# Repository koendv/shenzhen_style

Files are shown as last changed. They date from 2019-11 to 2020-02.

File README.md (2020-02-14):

# Shenzhen style

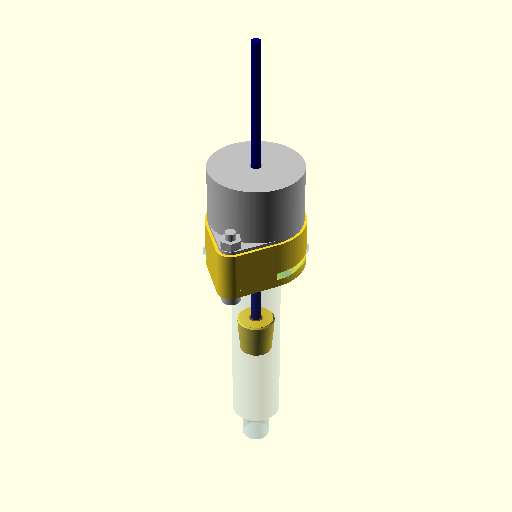
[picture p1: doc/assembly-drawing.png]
 

A 10cc glue dispenser. Designed to have a low number of pieces. Simple to solder, and easy to assemble. Plungers for [10cc Chinese generic](https://www.google.com/search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) , and 10cc Nordson. Adapter for mounting the glue dispenser on a CNC 3018 router.

Cutout view of the assembled dispenser: [3D assembly view](stl/assembly.stl)

## Bill of Materials
### 3D-Printed Workpieces
Workpieces printed in ABS using FDM:

- [body](stl/body.stl)
- [syringe holder](stl/syringe_holder.stl)
- [adapter for cnc 3018](stl/cnc3018_adapter.stl)
- [plunger](stl/plunger.stl)
- [insert_practice](stl/insert_practice.stl)

Leave part orientation as is when imported into PrusaSlicer. Designed to print without support.

### Dispenser Bill of materials

Quantity|Item
--------|----
1|[Robotdigg NC35-BYZ-120](https://www.robotdigg.com/product/1147/12V-35-captive-or-non-captive-linear-pm-stepper-motor) non-captive linear stepper, 7.5°/step
1|[M3 x 5.0mm O.D. x 6.0mm L threaded knurled brass insert](https://www.aliexpress.com/item/4000232858343.html)
2|[M4x25mm screw](https://www.aliexpress.com/item/4000197066058.html)
2|[M4 nut](https://www.aliexpress.com/item/32959149109.html)

Of course, you'll also need syringes. Some products, such as [Mechanic brand solder paste](https://www.google.com/search?q=Mechanic+XG-Z40+10cc+Syringe+Solder+Paste+Flux+Paste+Sn63%2FPb37), are sold in syringes, Luer needle included, ready to use. Or you can buy empty [10cc industrial glue dispenser syringes](https://www.aliexpress.com/item/33025919381.html) and fill them yourself.

## Assembly
- Set your soldering iron to the filament extrusion temperature used during 3D printing, about 255°C for ABS.
- As a test, take the workpiece [insert_practice](stl/insert_practice.stl) and place 4 heat-set inserts. 
- Put an M3 threaded brass insert in the [plunger](stl/plunger.stl).
- Screw the plunger on the stepper motor shaft.
### Hand-held
For the hand-held dispenser:
- Put the syringe in the [syringe holder](stl/syringe_holder.stl)
- Join stepper motor, [body](stl/body.stl), and syringe holder with the M4x25 screws.
- Connect the glue dispenser stepper motor to the controller board.

### CNC 3018 adapter
For the dispenser mounted in a CNC 3018 z-carriage:
- Put the syringe in the [adapter for cnc 3018](stl/cnc3018_adapter.stl).
- Join stepper motor, [body](stl/body.stl), and cnc 3018 adapter with the M4x25 screws.
- Put the dispenser in the CNC 3018 z-carriage. The dispenser has the same diameter as the router spindle, 42mm. Tighten the screws of the z-carriage very lightly, or not at all.
- Connect the glue dispenser stepper to the 3d-printer controller extruder (E0/E1).
- Dispensing glue is done by printing a g-code file, like a 3d printer.

## Controller
The controller is only needed if you wish to use the glue dispenser as a stand-alone, hand-held device. 

[Schematic and board layout at easyeda](http://easyeda.com/koendv/stepper-controller).

Quantity|Item
--------|----
1|[PCB](https://jlcpcb.com/)
1|[STM32F103C8T6 Blue Pill](http://www.aliexpress.com/item/32981849126.html)
1|[TMC2130 Silent Stepstick](https://www.aliexpress.com/item/32970150483.html)
1|[Mini dc-dc converter 24V to 5v](https://www.aliexpress.com/item/32796268715.html)
1|[0.96inch 128X64 I2C SSD1306 OLED WHITE/BLUE](https://www.aliexpress.com/item/32830523451.html)
1|[EC11 Rotary Encoder with Button](https://www.aliexpress.com/item/32915420023.html)
1|[3.5mm headphone jack](https://www.aliexpress.com/item/4000309078079.html)
1|[DC005 DC Power Jack 5.5mm dia, 2.5mm pin](https://www.aliexpress.com/item/4000034340966.html)
2|Pushbutton 6x6mm
1|Capacitor 47u/50V
1|4-Pin Male header (Dupont or JST XH-4AK)

*This is Work In Progress.*

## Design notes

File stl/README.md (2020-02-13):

3d-print the following files:

- [body](body.stl)
- [syringe holder](syringe_holder.stl)
- [plunger](plunger.stl)

If your cnc 3018 has a 45mm spindle, print this adapter:
- [adapter for mounting on cnc3018](cnc3018_adapter.stl)

If your cnc 3018 has a 52mm spindle, print this adapter:
- [adapter for mounting on cnc3018 with 52mm spindle](cnc3018_adapter_52mm.stl)

If you wish to practice threaded inserts first, also print:

- [insert practice](insert-practice.stl)

The directory also contains the following files:

- [assembly](assembly.stl) assembled hand-held dispenser

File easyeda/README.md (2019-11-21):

# PCB

pcb top pcb bottom 

[Gerber files](https://github.com/koendv/shenzhen_style/raw/master/easyeda/Gerber_stepper%20controller.zip) ready for pcb manufacturing. 

PCB project at [https://easyeda.com/koendv/stepper-controller](https://easyeda.com/koendv/stepper-controller)

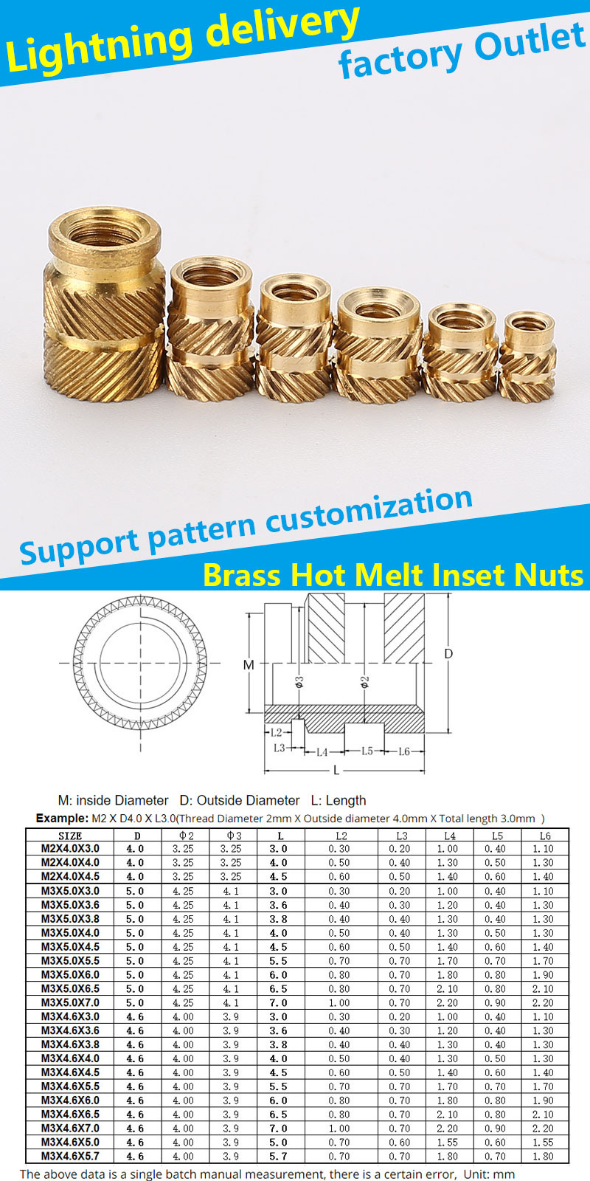
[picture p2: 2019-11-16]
doc/aliexpress-4000232858343.jpg

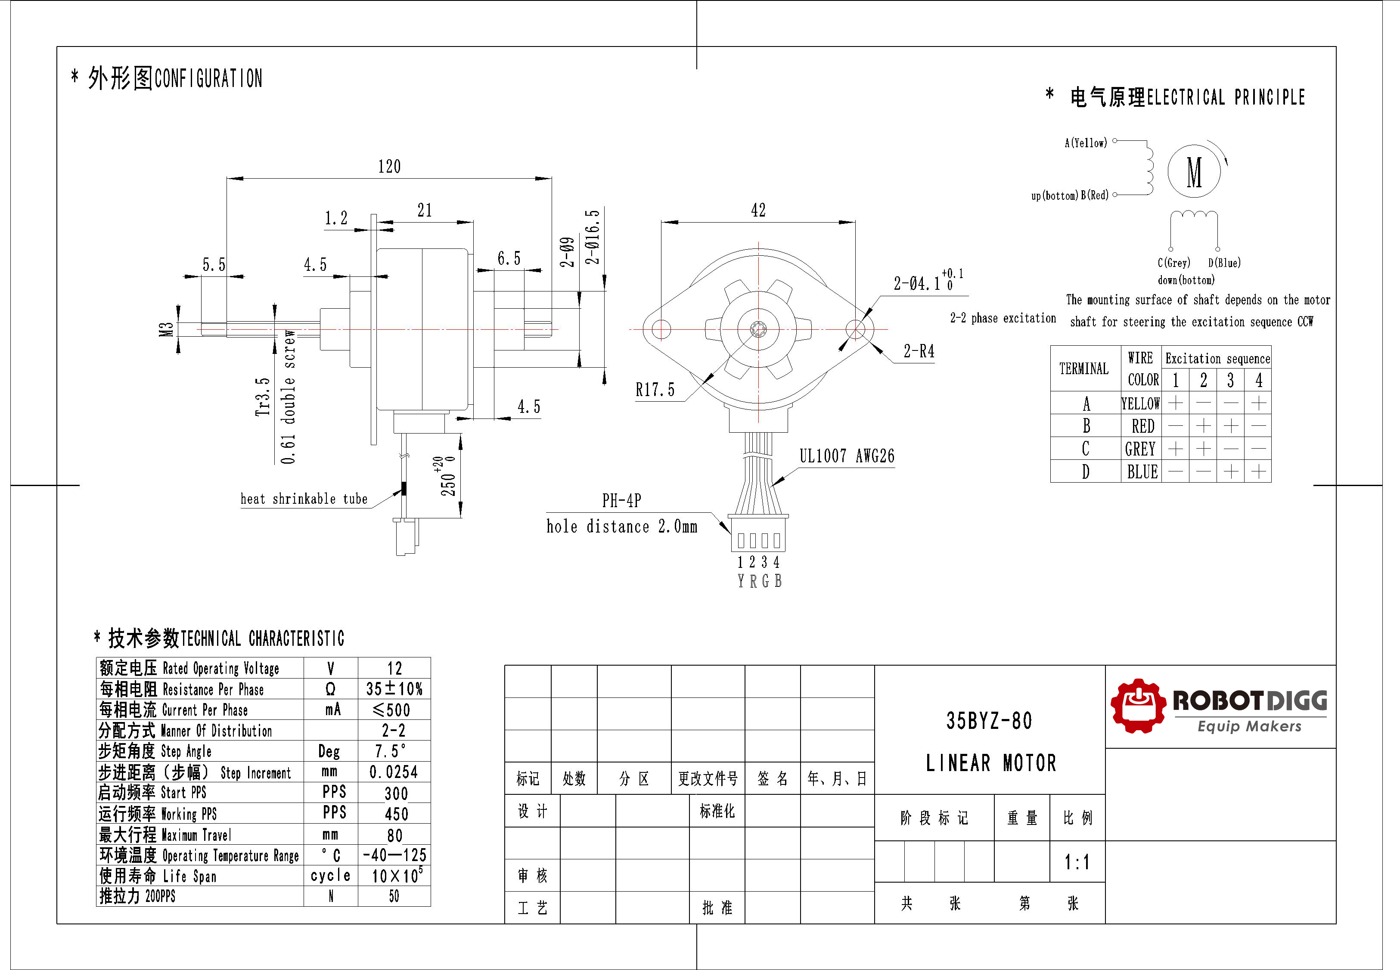
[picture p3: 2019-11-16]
doc/robotdigg-35-BYZ.jpeg

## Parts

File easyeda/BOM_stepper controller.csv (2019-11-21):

ID | Name | Designator | Footprint | Quantity | Manufacturer Part | Manufacturer | Supplier | Supplier Part
1 | Button-6x6x6mm | SW2,SW3 | SW-TH_4PIN-L6.00-W6.00 | 2 | Switch,6*6*6Plastic head,260G, 0.25mm,Straight line | BBJ | LCSC | C71836
2 | 0.96 128X64 I2C SSD1306 OLED WHITE/BLUE | U2 | 0.96 128X64 I2C SSD1306 OLED WHITE/BLUE | 1 | OLED 4PIN | WAVGAT | Aliexpress | 32830523451
3 | 47u/50V | C1 | CAP-D8.0XF3.5 | 1
4 | 3.5mm headphone jack | J1 | AUDIO-PJ320 | 1 | PJ320 headphone jack | BOOMELE | Aliexpress | 4000309078079
5 | MINI DC-DC CONVERTER 12-24V TO 5V 3A MAX | U3 | MINI DC-DC CONVERTER 12-24V TO 5V 3A MAX | 1 | QS-1205CME-3A | QSKJ | Aliexpress | 32796268715
6 | DC005 DC Power Jack 5.5mm dia, 2.5mm pin | P1 | DC005-2.5MM | 1 | Three-pin power interface DC005 2.5MMsocket Bagged RHOS | ReliaPro | Aliexpress | 4000034340966
7 | PWR_OFF | JP1 | 1X02 | 1
8 | TMC2130 stepstick | U1 | TMC2130 STEPSTICK \W DIAG0 DIAG1 VREF | 1 | TMC2130 stepstick |  | Aliexpress | 32970150483
9 | XH-4AK M | CN1 | XH-4A | 1 | - | Boom Precision Elec | LCSC | C146106
10 | STM32F103C8T6 BLUEPILL | U4 | STM32F103C8T6 BLUEPILL | 1 |  |  | Aliexpress | 32981849126
11 | EC11 Button | SW1 | EC11B-V | 1 | EC111012010H | Alps | Aliexpress | 32915420023

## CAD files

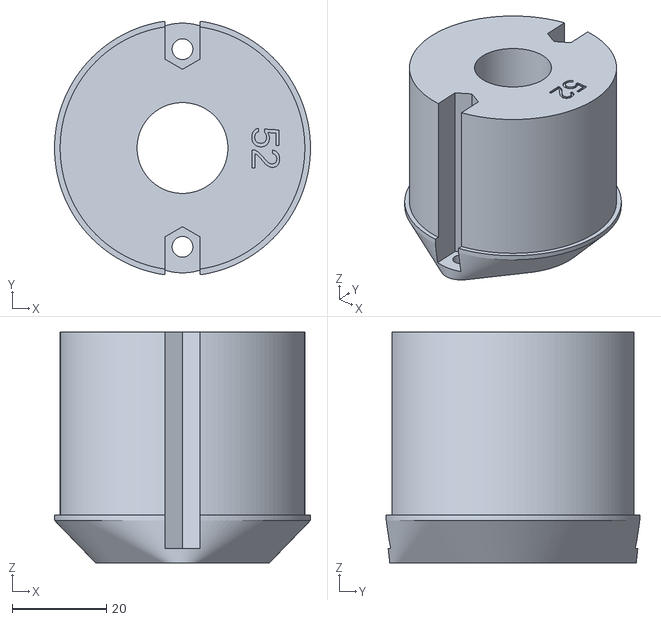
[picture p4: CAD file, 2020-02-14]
stl/cnc3018_adapter_52mm.stl
54.4 x 53.9 x 49.0

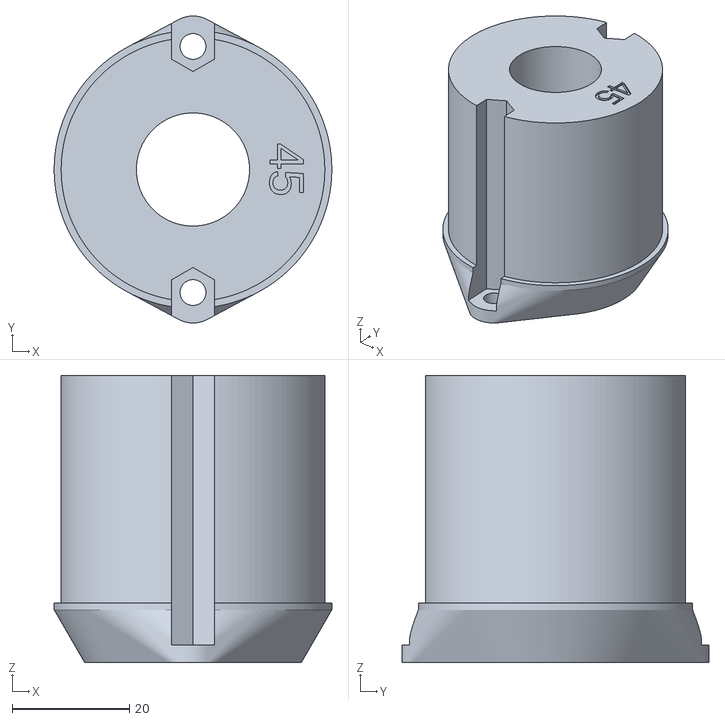
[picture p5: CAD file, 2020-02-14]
stl/cnc3018_adapter.stl
47.4 x 52.4 x 49.0

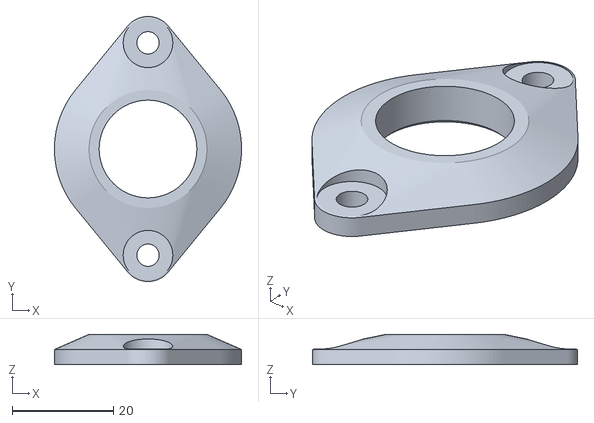
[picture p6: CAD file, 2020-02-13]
stl/syringe_holder.stl
37.0 x 52.4 x 6.00

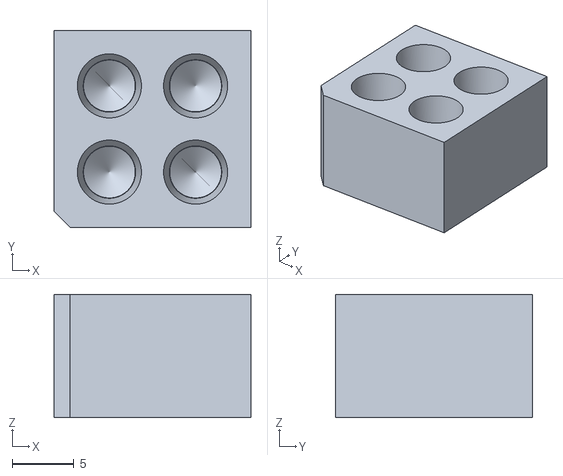
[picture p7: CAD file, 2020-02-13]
stl/insert-practice.stl
16.0 x 16.0 x 10.0

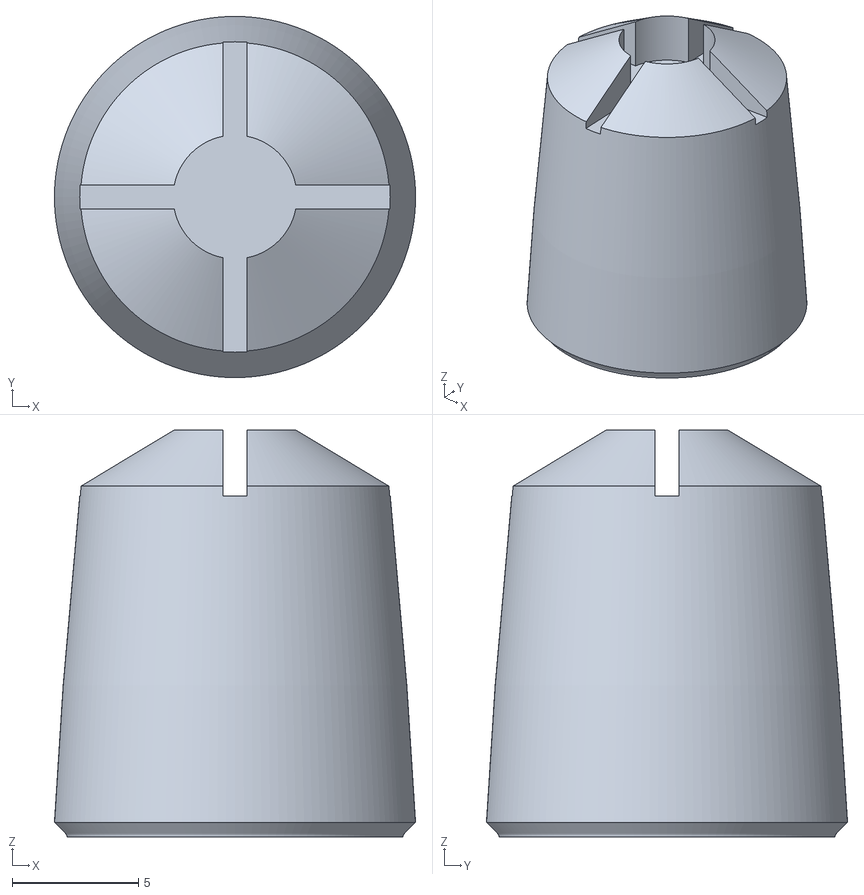
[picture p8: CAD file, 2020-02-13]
stl/plunger.stl
14.3 x 14.3 x 16.1

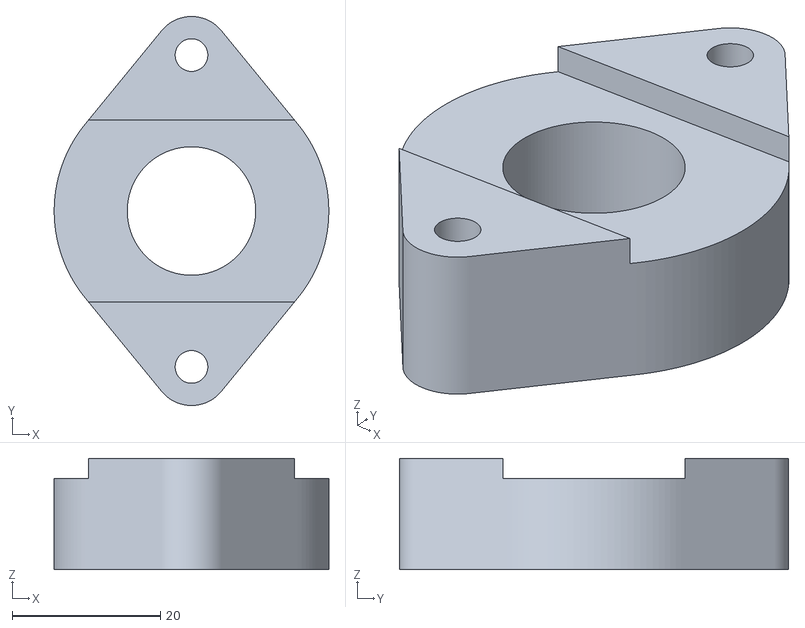
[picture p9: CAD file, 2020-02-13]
stl/body.stl
37.0 x 52.4 x 15.0

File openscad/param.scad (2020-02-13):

// process variables

clearance_fit = 0.4;      // approx. 2 x layer z height
tight_fit = 0.2;          // approx. half clearance fit
tweak=0.2;                // tweak for fdm printer with 0.4mm nozzle
tweak_insert=0.2;         // tweak threaded insert hole to compensate for printer tolerance. bigger value = bigger hole.
min_wall_thickness = 2.0; // minimum desired wall thickness, conservative value
chamfer = 0.5;            // chamfer to avoid fdm elephant's foot

// general variables
//$fn = 128; // high resolution for rendering
$fn = 32; // low resolution when designing
eps1 = 0.001; // "epsilon", small value to avoid collisions
eps2 = 2 * eps1;

// Choose syringe model
include <syringe-10cc-generic.scad>;
//include <syringe-10cc-bd.scad>;
//include <syringe-10cc-nordson-wiper.scad>;

// Choose canstack stepper model
// Robotdigg NC35-BYZ-120
// https://www.robotdigg.com/product/1147/12V-35-captive-or-non-captive-linear-pm-stepper-motor
include <stepper-robotdigg-35-byz.scad>

// body dimensions
body_height = 15.0;

// syringe holder
syringe_holder_base_height = 3.0;
syringe_holder_total_height = 6.0;

// adapter for cnc3018
cnc_zcarriage_dia1 = 45.0; // diameter of spindle hole. Common values: 45mm, 52mm.
cnc_zcarriage_h1 = 40.0;   // height

// not truncated

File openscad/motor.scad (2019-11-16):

include <param.scad>
include <util.scad>

/*
 * model of a can-stack non-captive linear stepper 
 */

module motor (position = 0.5) {
    difference() {
        union() {
            // stepper base plate
            linear_extrude(height = stepper_base_thickness)
            difference() {
                hull() {
                    twice() circle(d = stepper_length - stepper_screw_spacing);
                    circle(d = stepper_width);
                }
                twice() circle(d = stepper_screw_dia);
            }
            
            // stepper body
            translate([0, 0, stepper_base_thickness])
            cylinder(d = stepper_width, h = stepper_height );
            
            // stepper front cap
            translate([0, 0, -stepper_bottom_height])
            cylinder(d = stepper_bottom_dia, h = stepper_bottom_height);
        }
        cylinder(d = leadscrew_dia + 2 * clearance_fit, h = leadscrew_length, center = true);
    }
    
}

module leadscrew() {
    // leadscrew
    translate([0, 0, leadscrew_tip_length])
    cylinder(d = leadscrew_dia, h = leadscrew_length);
    
    // leadscrew threaded tip
    cylinder(d = leadscrew_tip_dia, h = leadscrew_tip_length + eps1);
}

if (0) {
    motor();
    translate([0, 0, -leadscrew_length/2])
    leadscrew();
}

//motor();
//leadscrew();
// not truncated

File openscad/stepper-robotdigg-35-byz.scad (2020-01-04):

// Robotdigg NC35-byz-120, 35mm, 7.5 degree/step, 12V
// price: $14.00
// https://www.robotdigg.com/product/1147/12V-35-captive-or-non-captive-linear-pm-stepper-motor

stepper_screw_spacing = 42.0;
stepper_screw_dia = 4.4; // M4 screws
stepper_length = 50.0;
stepper_width = 35.0;
stepper_height = 21.0;
stepper_base_thickness = 1.2;

stepper_bottom_dia = 16.5;
stepper_bottom_height = 11.0; // 6.5 + 4.5 on the drawing

leadscrew_dia = 3.5;
leadscrew_length = 115.0;
leadscrew_tip_dia = 3.0;
leadscrew_tip_length = 5.5;

// not truncated

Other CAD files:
openscad/assembly.scad
openscad/attic/syringe-10cc-bd.scad
openscad/attic/syringe-10cc-nordson-flat.scad
openscad/attic/syringe-5cc-generic.scad
openscad/attic/syringe-5cc-nordson-wiper.scad
openscad/body.scad
openscad/generate.scad
openscad/insert-practice.scad
openscad/plunger.scad
openscad/syringe-10cc-generic.scad
openscad/syringe-10cc-nordson-wiper.scad
openscad/syringe.scad
openscad/threaded-insert.scad
openscad/util.scad

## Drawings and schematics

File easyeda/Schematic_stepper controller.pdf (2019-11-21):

# E D G² G² G¹ G¹

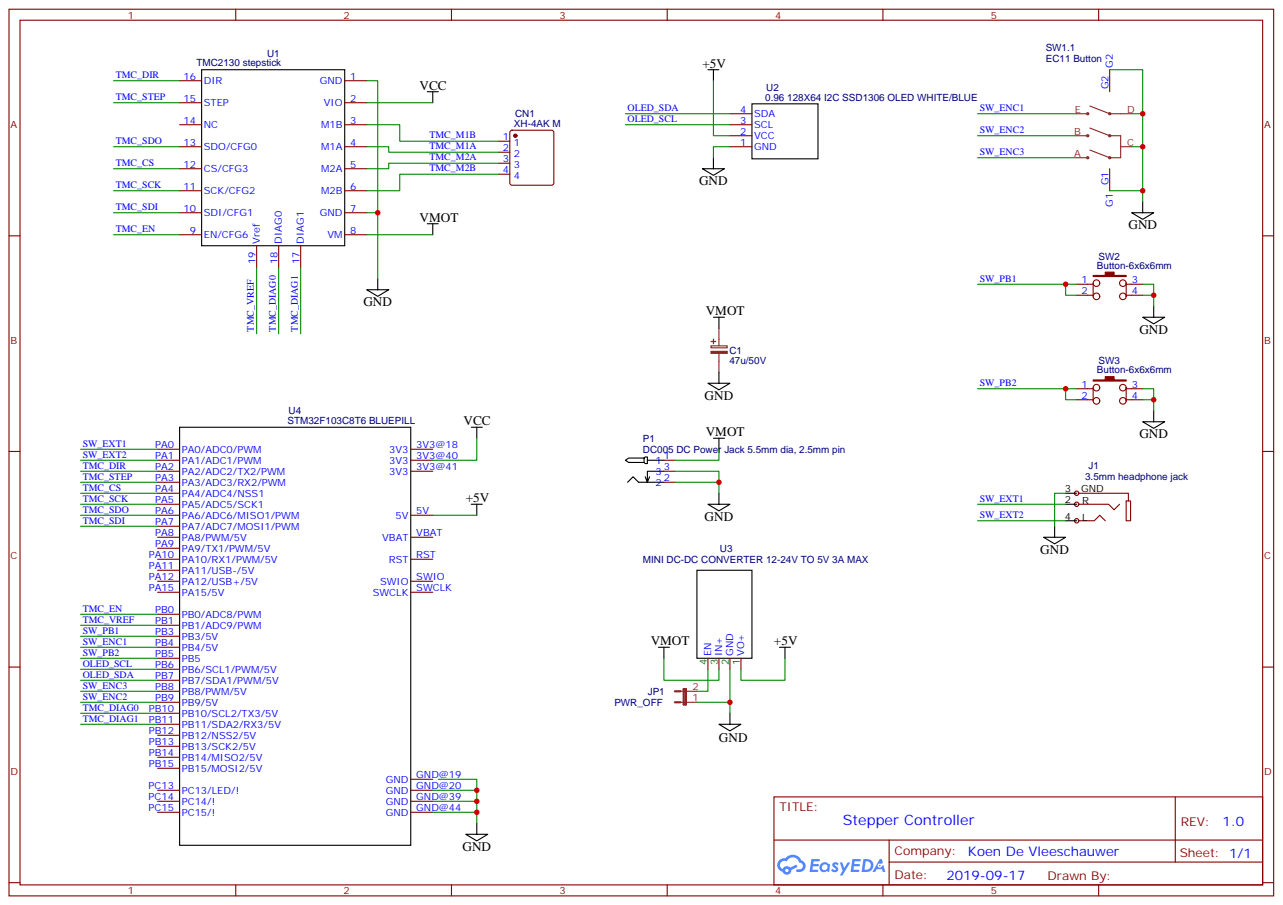
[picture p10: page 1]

PA0/ADC0/PWM PA0
PA15/5V PA15 PA12/USB+/5V PA12 PA11/USB-/5V PA11 PA10/RX1/PWM/5V PA10 PA9/TX1/PWM/5V PA9 PA8/PWM/5V PA8 PA7/ADC7/MOSI1/PWM PA7 PA6/ADC6/MISO1/PWM PA6 PA5/ADC5/SCK1 PA5 PA4/ADC4/NSS1 PA4 PA3/ADC3/RX2/PWM PA3 PA2/ADC2/TX2/PWM PA2 PA1/ADC1/PWM PA1

VBAT
RST
SWCLK SWCLK SWIO SWIO

MINI DC-DC CONVERTER 12-24V TO 5V 3A MAX

PB15/MOSI2/5V PB15 PB14/MISO2/5V PB14 PB13/SCK2/5V PB13 PB12/NSS2/5V PB12 PB11/SDA2/RX3/5V PB11 PB10/SCL2/TX3/5V PB10 PB9/5V PB9 PB8/PWM/5V PB8 PB7/SDA1/PWM/5V PB7 PB6/SCL1/PWM/5V PB6 PB5 PB5 PB4/5V PB4 PB3/5V PB3 PB1/ADC9/PWM PB1 PB0/ADC8/PWM PB0

Company: Koen De Vleeschauwer

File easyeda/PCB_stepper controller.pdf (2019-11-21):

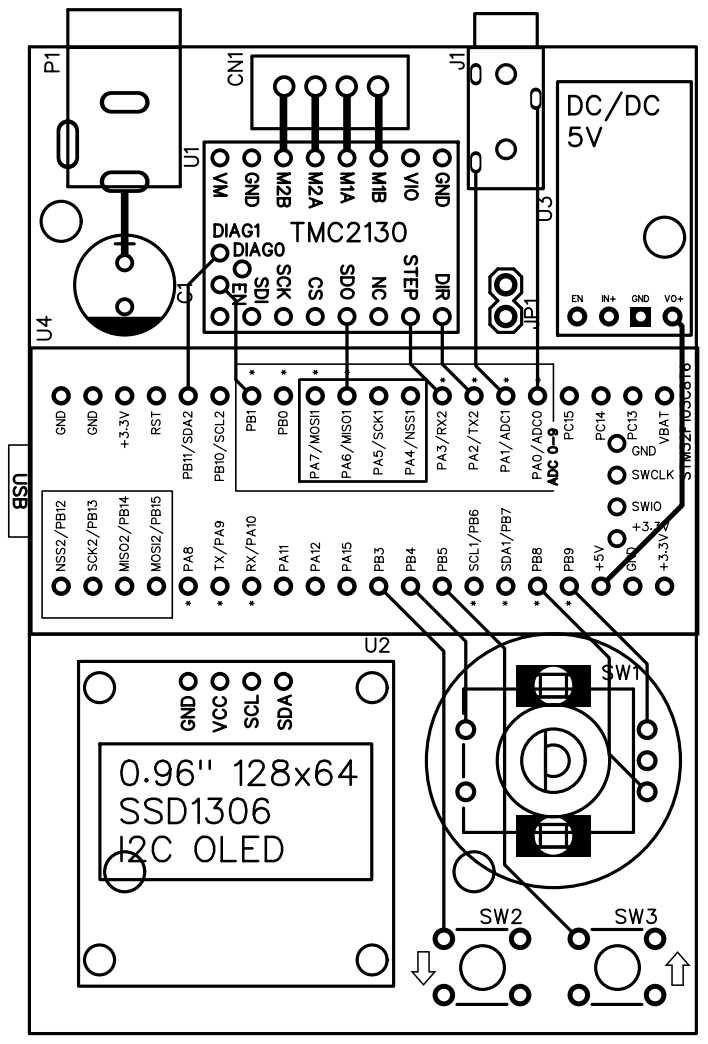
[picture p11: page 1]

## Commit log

2019-11-16 first print
    [assembly.scad, body.scad, generate.scad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]
2019-11-20 first pcb
2019-12-31 dual nema8
    [cnc3018.scad]
2020-01-04 stepper screws
    [cnc3018_raspi.scad, cnc3018_zcarriage.scad, stepper-robotdigg-35-byz.scad]
2020-01-31 remove bd
    [syringe-10cc-bd.scad]
